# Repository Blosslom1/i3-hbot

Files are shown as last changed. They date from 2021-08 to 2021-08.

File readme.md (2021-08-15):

# 3Dimension Printer

## 机器简介

本项目中含有三台打印机结构。依次迭代更新。

i3进程&远程挤出结构，家用级，适合慢速打印，快速会出现较多震纹，精度普通最高达到0.1mm。

主控芯片采用的mega2560芯片，固件改写的为marlin1.1.9

驱动使用4个A4988（双z并联），可以根据自己经济能力改用TMC2209或闭环驱动。

hbot，高精工业级，可以实现高速打印在影响质量较小的情况下是i3速度的4-8倍速，最高精度可达0.025mm。主控是32位LPC1768，固件升级为marlin2.0.x

本hbot打印机是由上一版本i3结构改造，设计理念围绕低成本，高性能 ，在采购原始材料尽量使用的未加工的材料成本较低。

制作流程请跟随本文指示。

### 第一步

参看原始设计图，使用solid work2019，打开根目录的装配体1，看懂机械原理有大概机器布局印象后进行材料采购。

### 第二步

使用excel打开根目录BOM表。名称为i3_BOM（由于零件细碎未整理hbot的bom，仅仅增加几个2020铝型材大体没有怎么变）。

### 第三步

打印件定制，设计图纸的非标零件都需要定制，使用FMD打印定制即可，可以进入hbot打印件中查看需要定制的零件种类。

### 第四步

主板如果使用mega2560，使用arduino(先安装程序固件\arduino-1.8.13-windows.exe)写入程序固件中的程序程序目录：程序固件\Marlin-2.0.x\Marlin\Marlin.ino

主板使用skr等32位主板，使用卡烧录，firmware.bin文件，文件已经调试编译好可以直接烧录。

## 暂停更新

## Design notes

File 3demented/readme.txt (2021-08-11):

X固定×1
X固定右×1
Y光轴固定×4
Y同步轮固定×1
Y轴步进电机固定×1
Z轴固定×2
热床底板固定×4
挤出机支架×1
熔融喷头固定×1
Y固定上×2

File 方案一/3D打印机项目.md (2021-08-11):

# 3D打印机项目

## 打印机类型

熔融沉积型打印机（FDM）

## 设计建模

建模软件使用的是solid works 2018，用二维图形生成三维图形。

### 支架型材

#### x轴铝型材

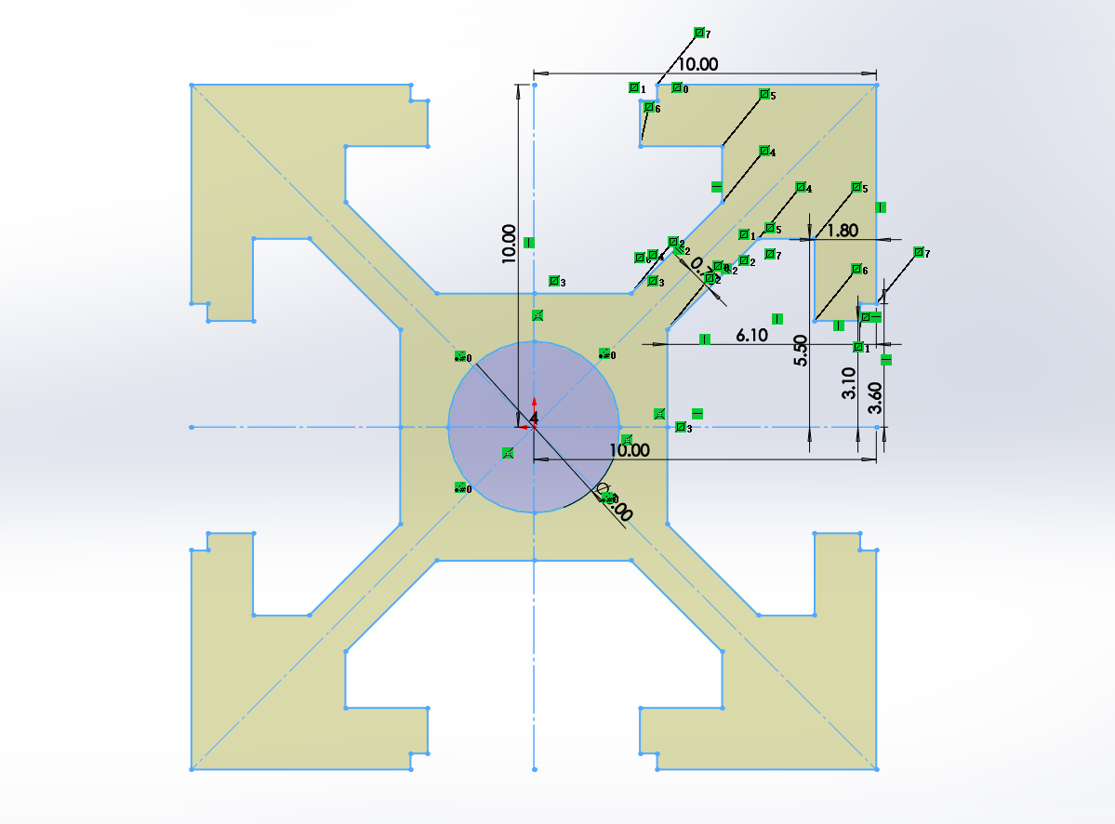
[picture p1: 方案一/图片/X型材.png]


规格如图（规格全部参考模型源文件，项目地址），使用拉伸凸台生成立体零件，拉伸长度是245mm

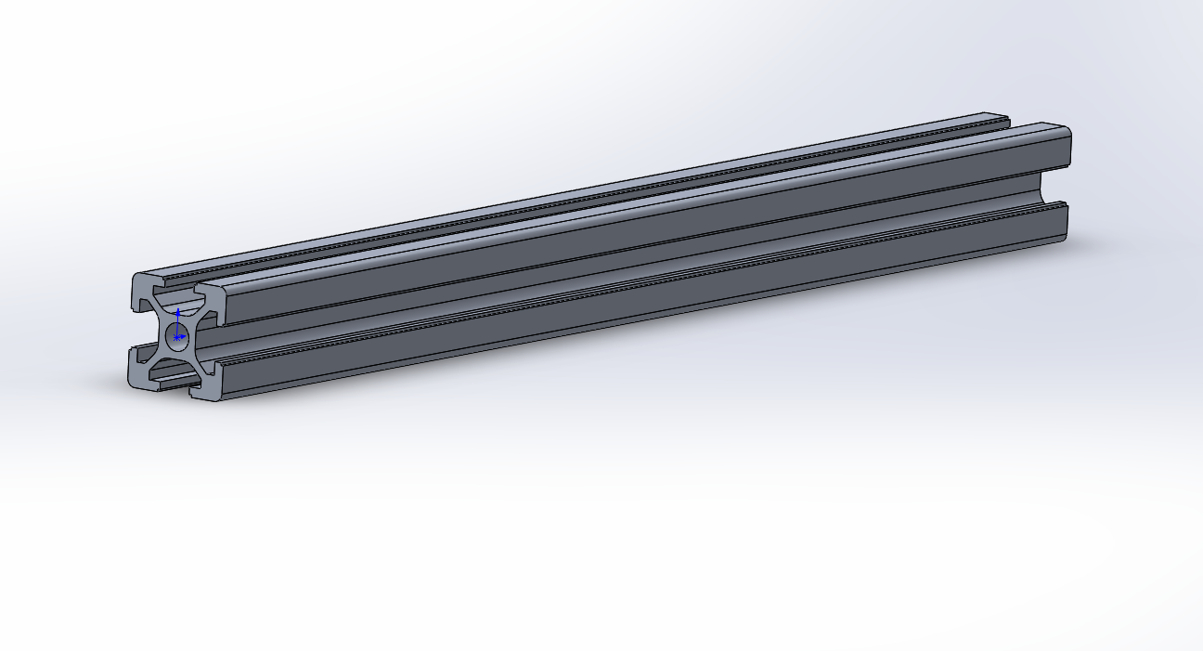
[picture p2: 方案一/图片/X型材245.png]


#### y轴铝型材

同x轴型材，拉伸长度是385mm

#### z轴铝型材

同x轴型材，拉伸长度是310mm

#### x光轴

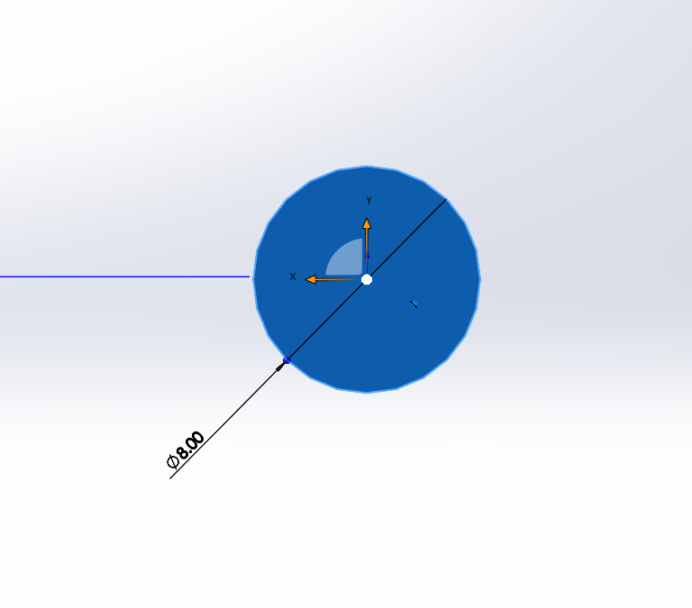
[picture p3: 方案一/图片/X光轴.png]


规格如图，使用拉伸凸台生成立体零件，拉伸长度是320mm

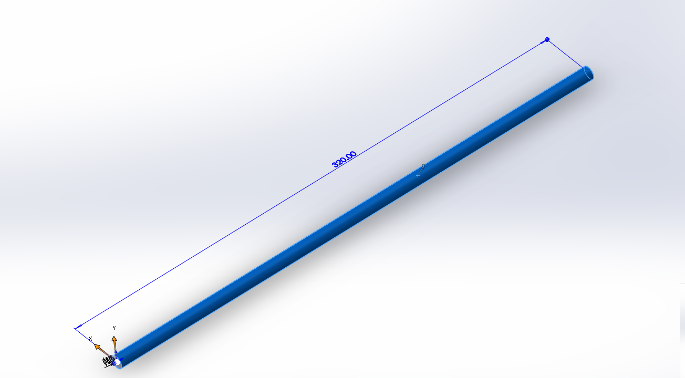
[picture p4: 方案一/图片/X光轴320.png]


#### y光轴

同x光轴，拉伸长度是380mm

#### z光轴

同x光轴，拉伸长度是345mm

#### z丝杆

长度305mm

#### 热床平台

下图为热床草图，厚度是3mm

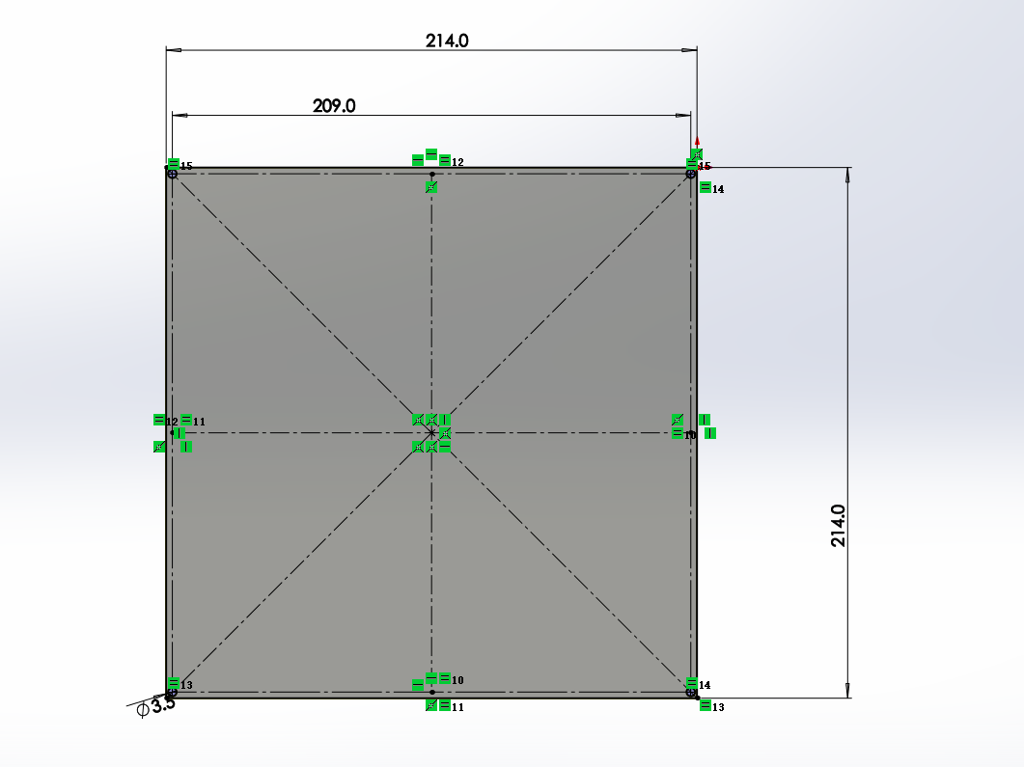
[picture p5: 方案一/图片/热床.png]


下图为热床地板草图，厚度是2.5mm

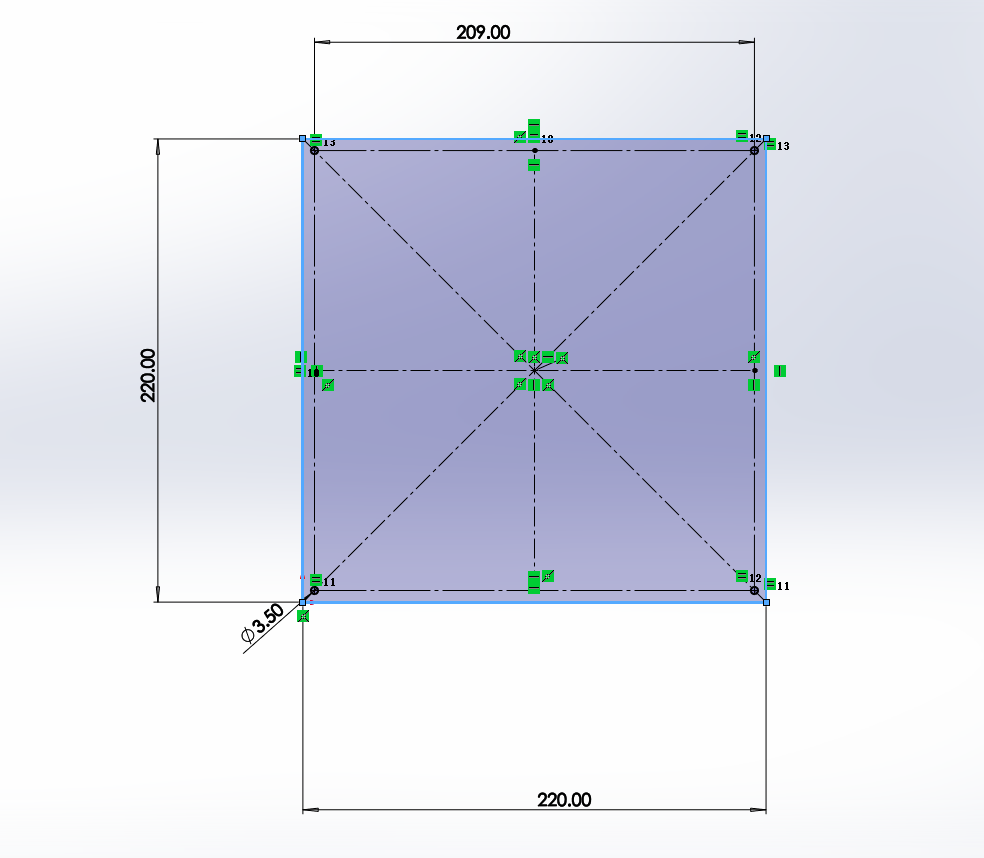
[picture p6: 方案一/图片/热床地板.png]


#### 角码

角码中间位置，L型型材，拉伸长度是20mm

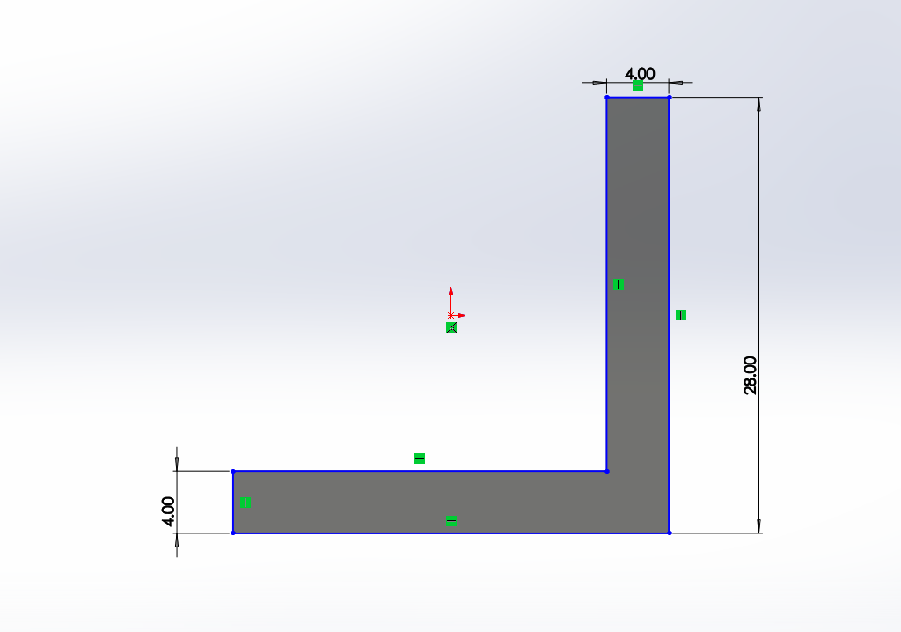
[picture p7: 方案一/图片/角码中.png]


角码侧边位置如图尺寸，两边通过镜像建立，拉伸长度是3.5mm

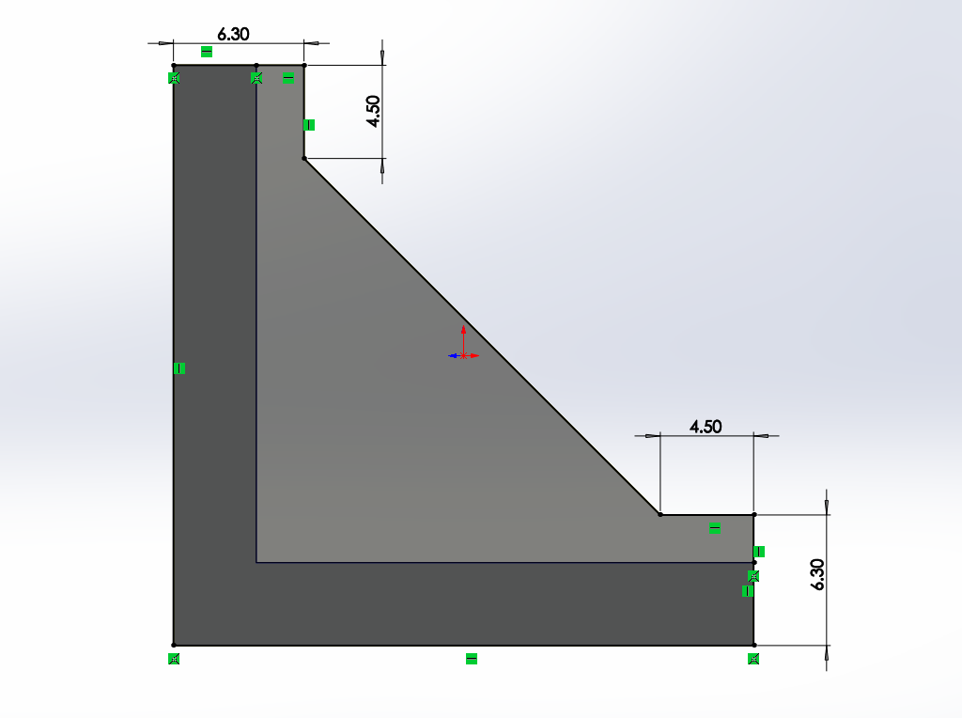
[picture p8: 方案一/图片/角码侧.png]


角码底和后面是一样的，拉伸切除，草图如下

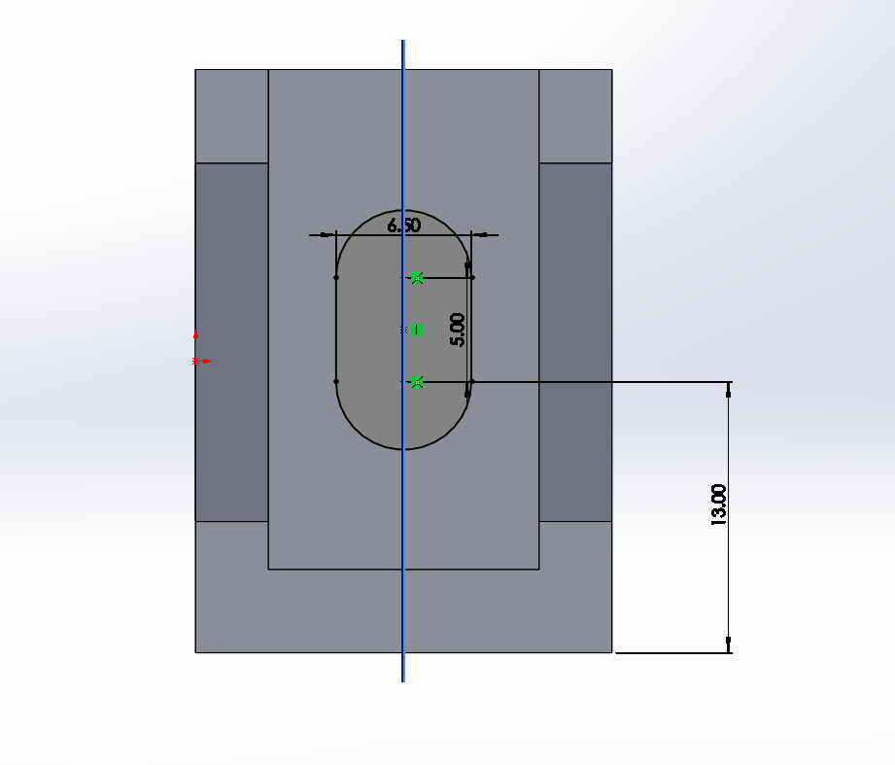
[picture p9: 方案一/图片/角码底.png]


整体图如下：

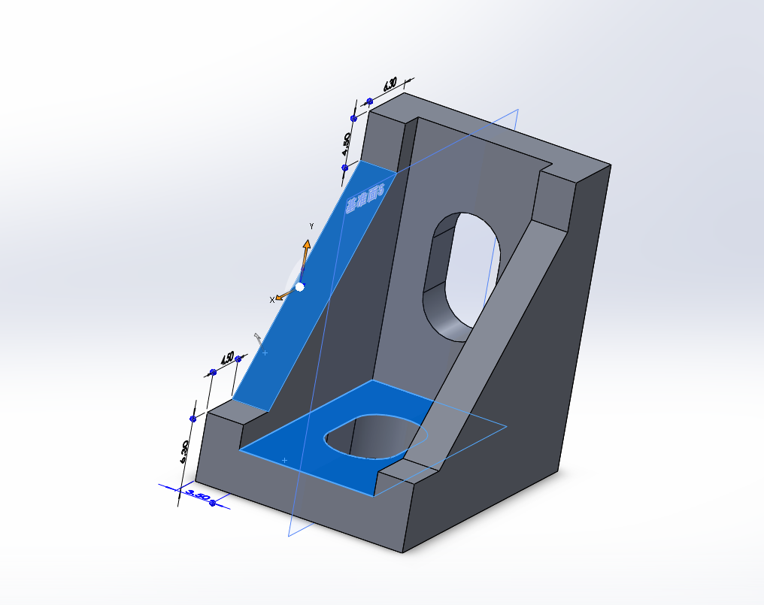
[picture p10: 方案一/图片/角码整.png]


#### 联轴器

联轴器是由一个圆柱体组成，中空，阶梯规格，草图如下，拉伸25mm

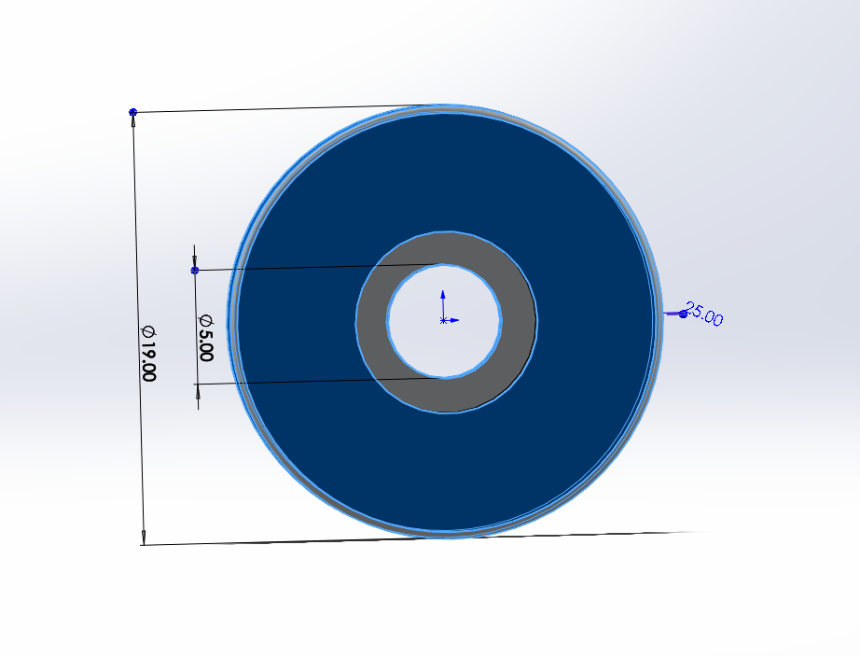
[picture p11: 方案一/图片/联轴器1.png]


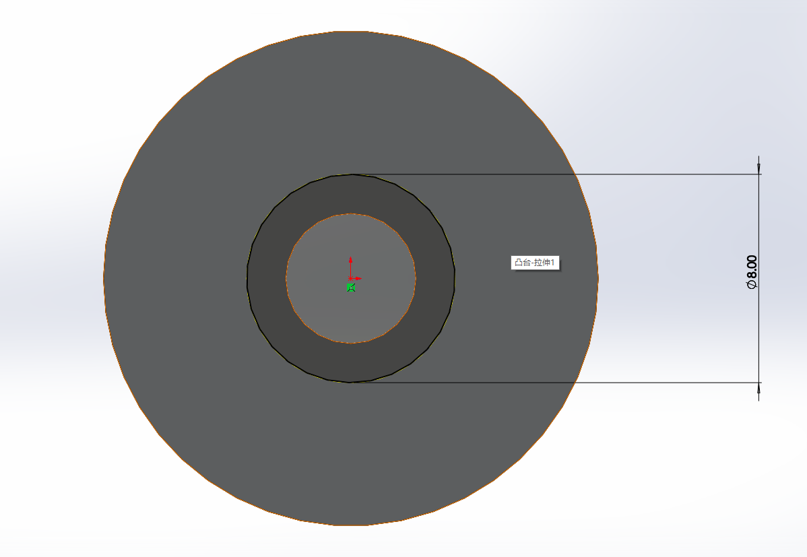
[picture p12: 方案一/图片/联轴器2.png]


整体如下图：

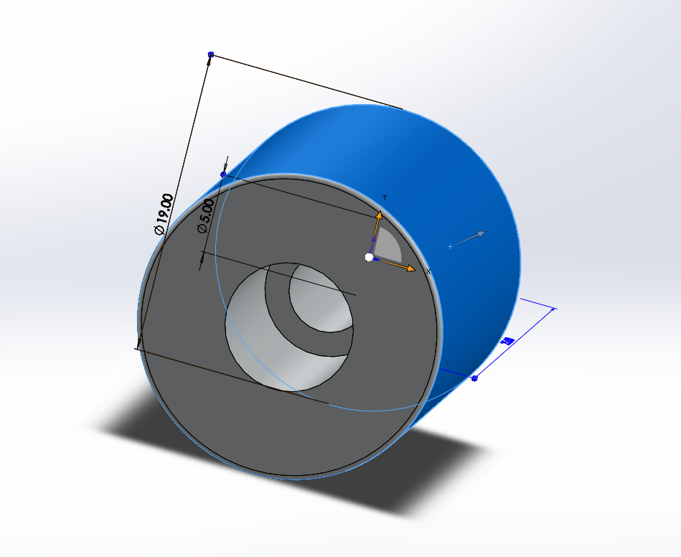
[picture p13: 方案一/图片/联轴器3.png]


#### 同步轮

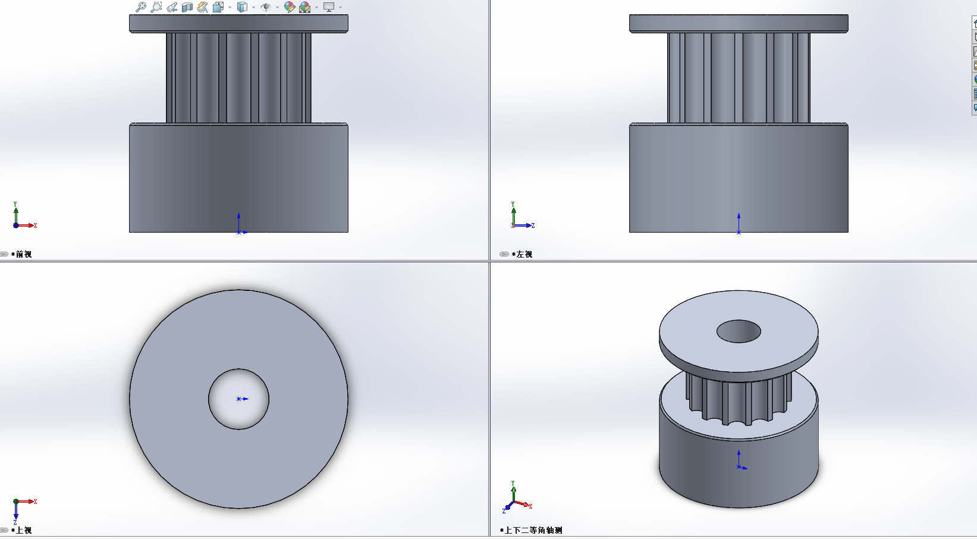
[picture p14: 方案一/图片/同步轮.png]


#### LM8UU

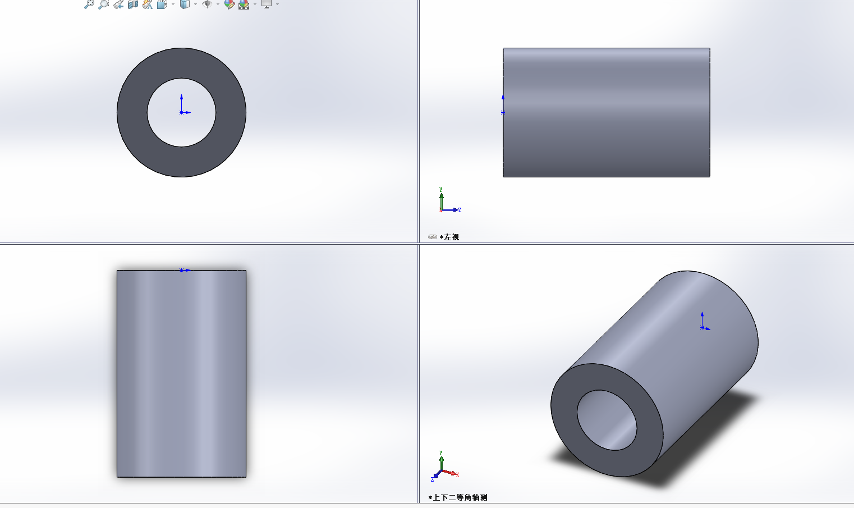
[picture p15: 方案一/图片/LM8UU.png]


#### 丝杆螺母

丝杆螺母，参考图。

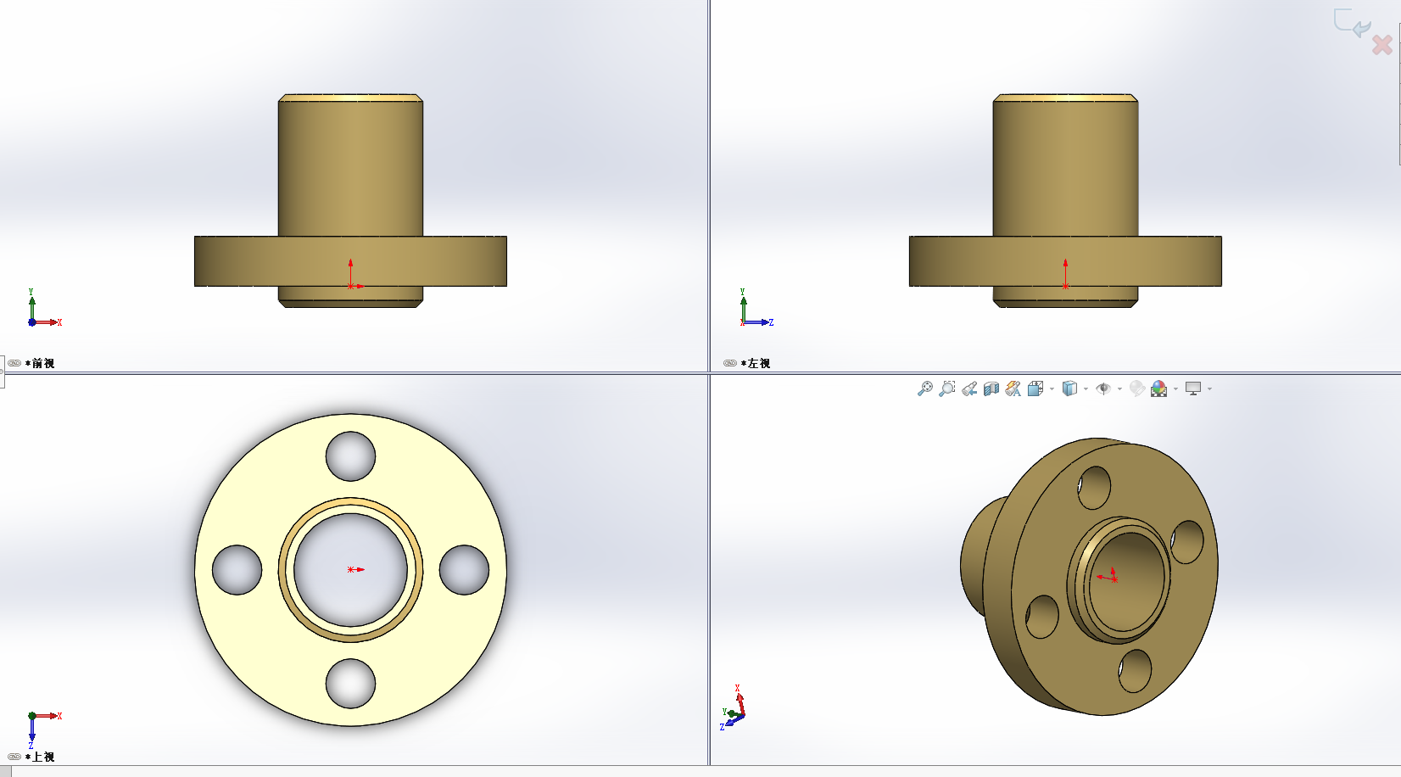
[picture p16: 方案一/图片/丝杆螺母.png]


#### 42步进电机

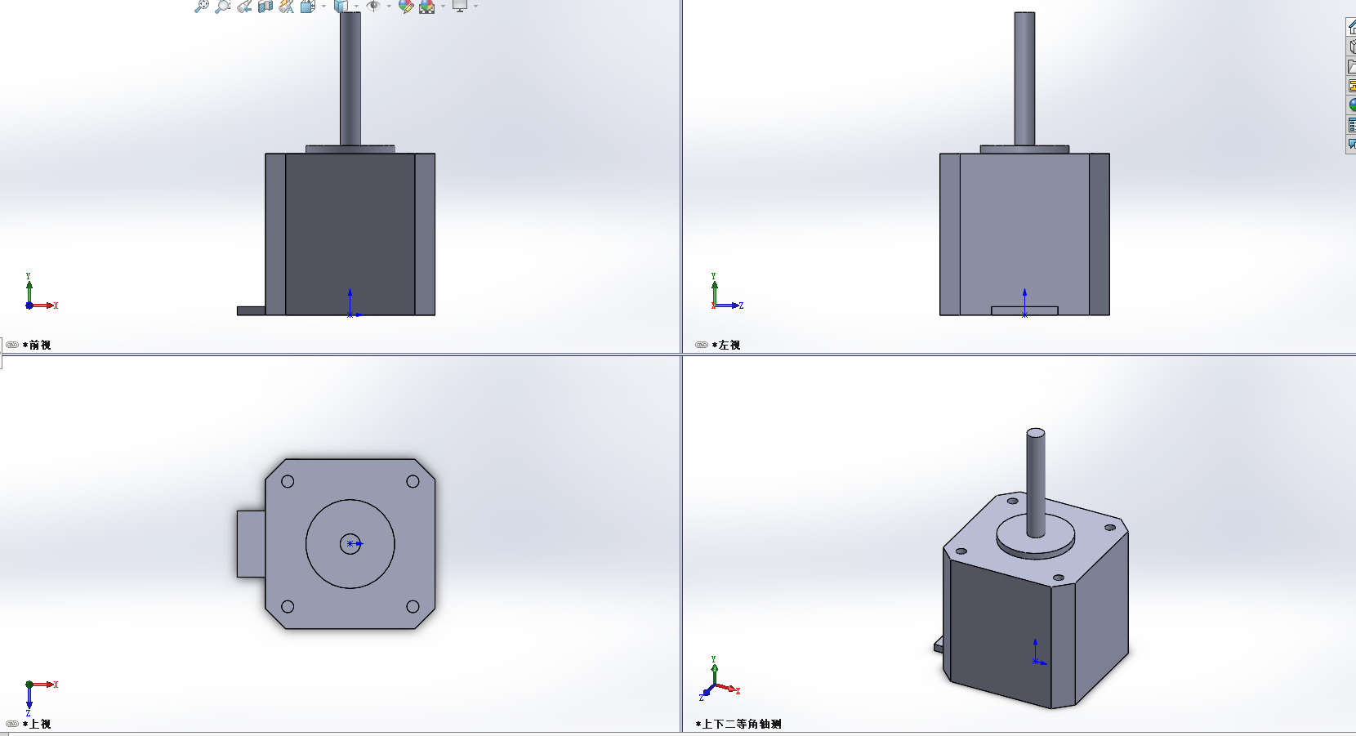
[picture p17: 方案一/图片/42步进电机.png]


#### 挤出机

下图是MK8底板。

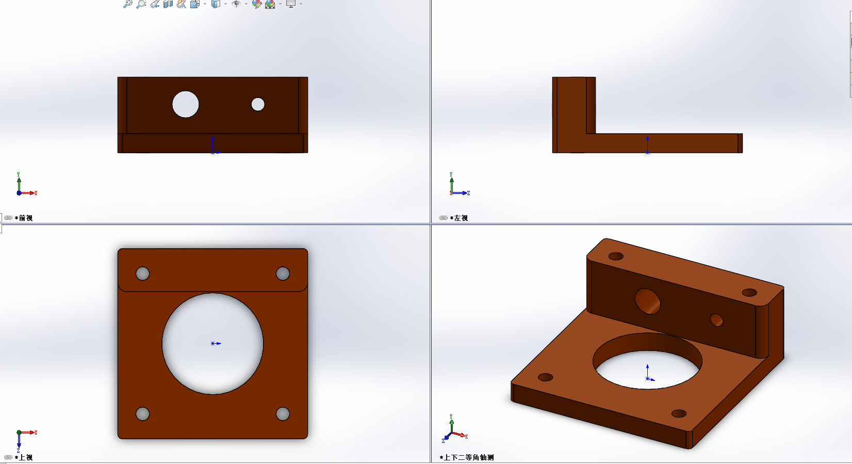
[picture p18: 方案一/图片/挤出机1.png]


下图是MK8压杆

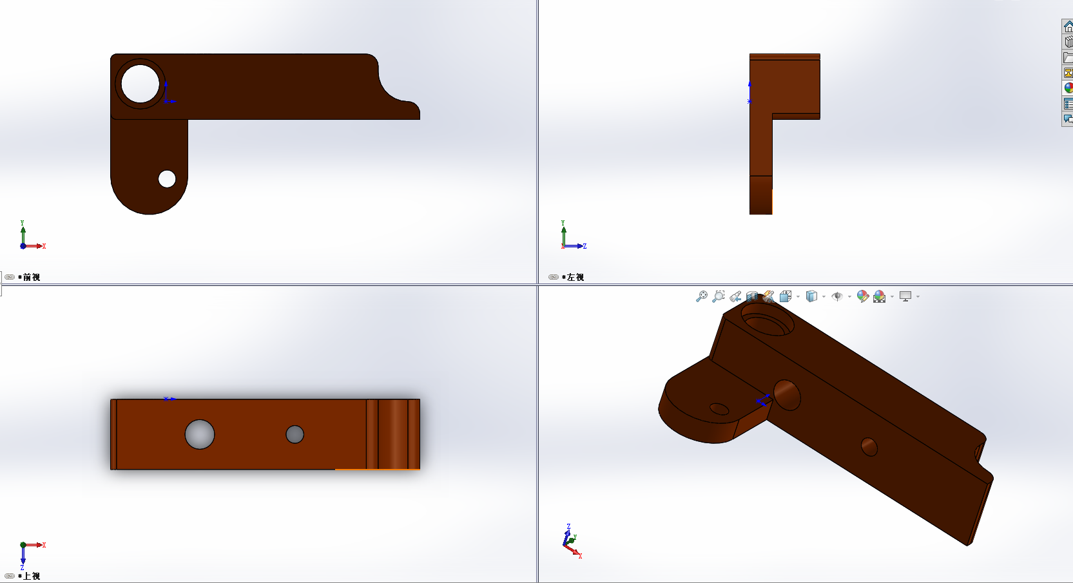
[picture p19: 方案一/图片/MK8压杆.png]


下图是MK8散热片

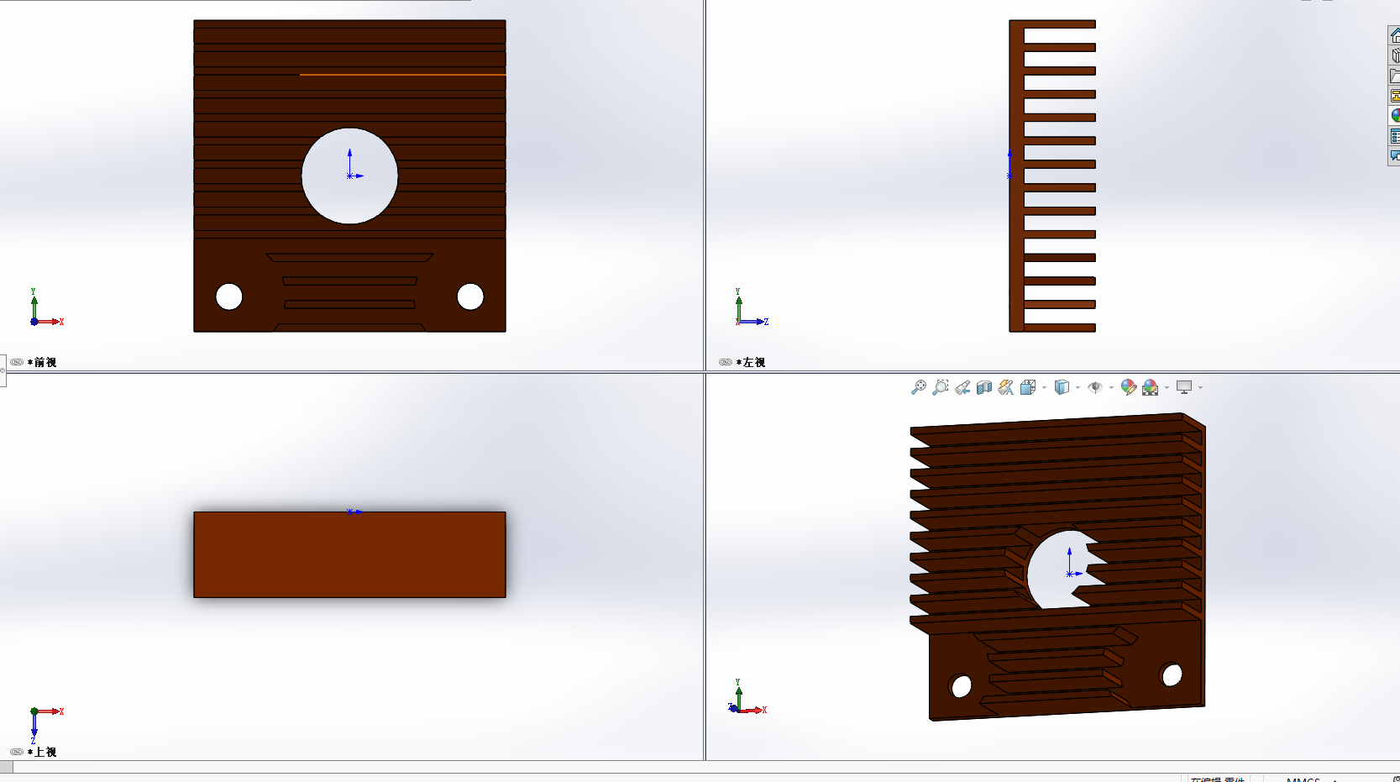
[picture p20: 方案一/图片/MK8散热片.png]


#### 喉管

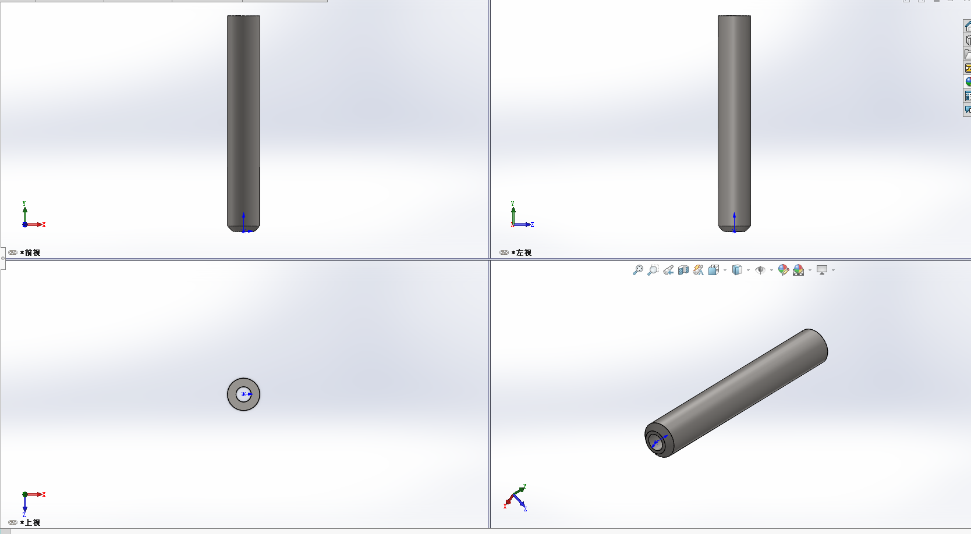
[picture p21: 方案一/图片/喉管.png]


#### 喉管散热片

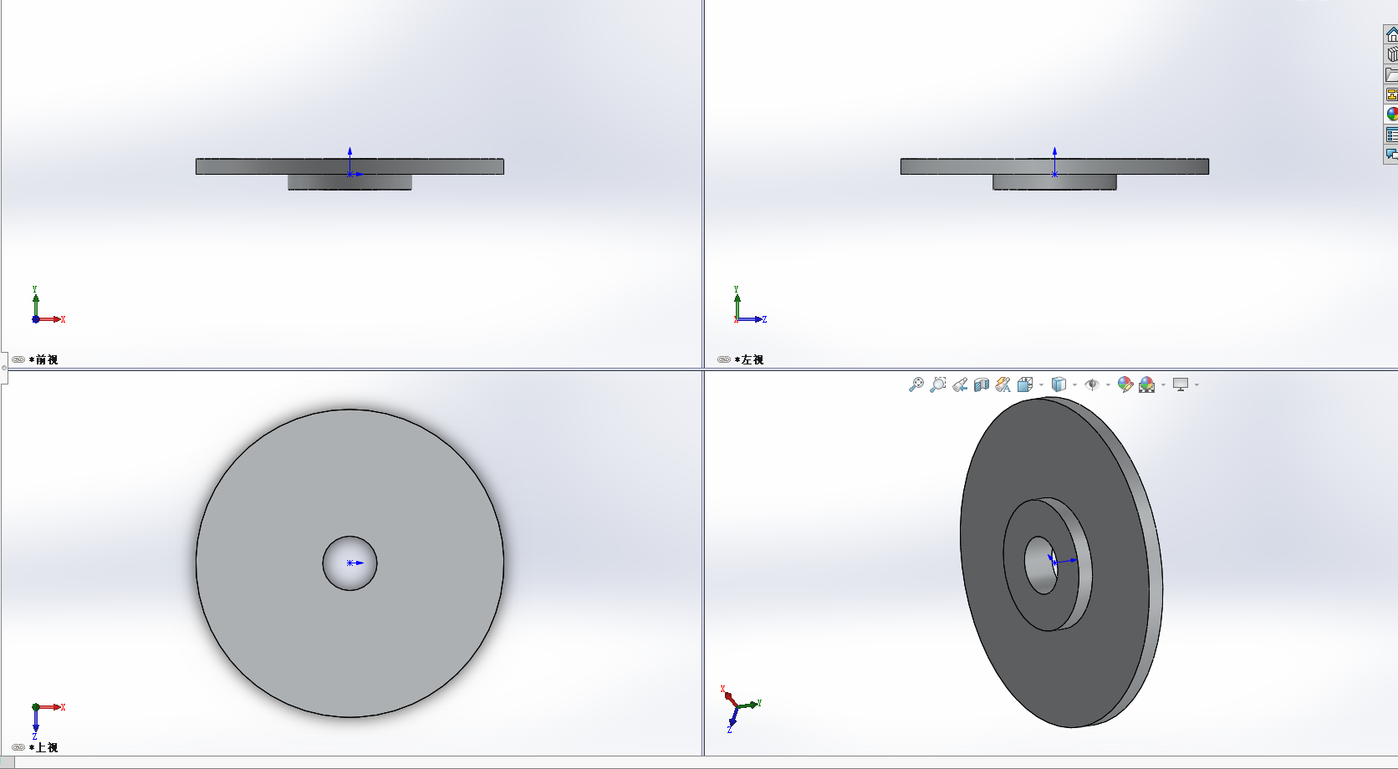
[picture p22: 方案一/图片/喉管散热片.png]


#### 固定

下图是Y光轴固定

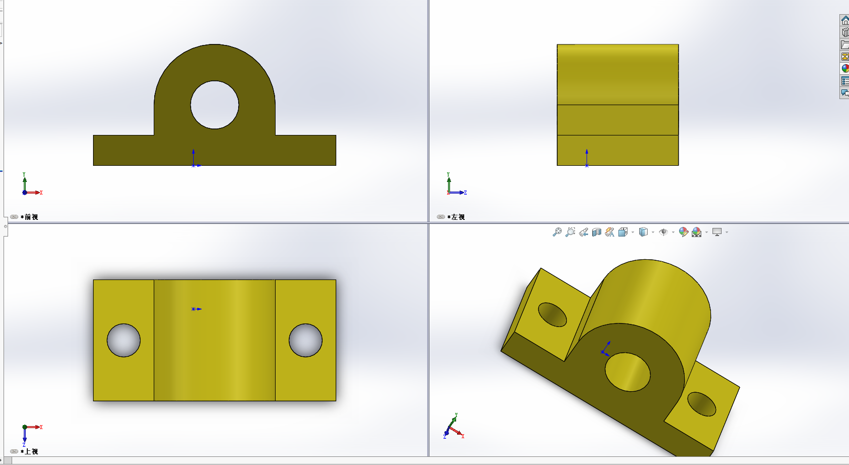
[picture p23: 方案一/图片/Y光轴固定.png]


下图是热床底板固定

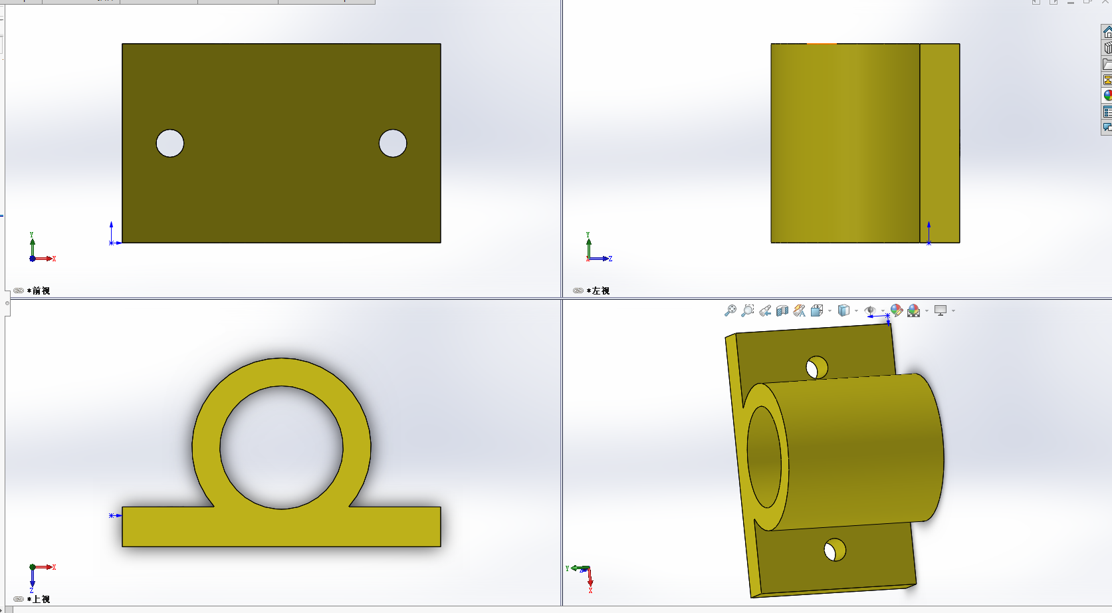
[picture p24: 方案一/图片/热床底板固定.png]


#### 铝加热块



#### 喷口



### 零件总装

使用装配界面将上面设计好的零件进行装配。

需要零件有X型材2个，角码4个，横梁型材1个，热床平台1个，光轴380两个，光轴固定4个，热床底板固定4个，LM8UU4个。下列是他们的几何位置关系。

{% hideBlock 查看几何位置关系 %} 

重合2X型材(1),Y型材(1)

重合5X型材(1),Y型材(1)

重合6X型材(1) ,Y型材(1)

重合8X型材(1),角码(1)

重合9Y型材(1),角码(1)

重合10X型材(1),角码(1)

重合15X型材(1) ,Y型材(2)

重合21X型材(1),Y型材(2)

重合22X型材(1),Y型材(2)

人重合24Y型材(2),角码(2)

重合25X型材(1),角码(2)

重合26Y型材(2) ,角码(2)

重合27角码(1),角码(2=

重合30Y型材(1),X型材(2)

重合31Y型材(1),X型材(2)

重合32Y型材(1),X型材(2)

重合33角码(4),X型材(2)

重合34Y型材(1),角码(4)

重合35Y型材(1),角码(4)

重合36角码(3) ,X型材(2)

重合37Y型材(2),角码(3)

重合38V型材(2),角码(3)

重合39Y型材(1),Z型材(1)

重合40Y型材(1),7型材(1)

重合43V型材(2),Z型材(2)

重合44Y型材(2),Z型材(2)

重合47Z型材(1),Z型材(2)

重合48Z型材(1),横梁型材(1)

重合49Z型材(1),横梁型材(1)

重合51Z型材(1),角码(5)

重合52横梁型材(1),角码(5)

重合53Z型材(1),角码(5)

重合55横梁型材(1),角码(6)

重合56Z型材(2),角码(6)

重合57Z型材(2),角码(6)

距离1横梁型材(1),Z型材(1)

重合58X型材(1),Y光轴固定(1)

重合59 X型材(1),Y光轴固定(1)

同心1Y光轴380(1),Y光轴固定(1)

重合62Y光轴380(1),Y光轴固定(1)

重合63X型材(1),Y光轴固定(2)

重合64X型材(1),Y光轴固定(2)

同心2Y光轴固定(2),Y光轴380(2)

重合66Y光轴固定(2),Y光轴380(2)

重合69 X型材(2),Y光轴固定(4)

重合70X型材(2),Y光轴固定(4)

同心3Y光轴380(2) ,Y光轴固定(4)

重合72X型材(2),Y光轴固定(5)

重合73X型材(2),Y光轴固定(5)

同心4Y光轴380(1),Y光轴固定(5)

同心5Y光轴380(2),LM8UU(3=

同心6Y光轴380(2),LM8UU(4)

同心7Y光轴380(1),LM8UU(2)

同心8Y光轴38O(1),LM8UU(1)

重合76 LM8UU(2),热床底板固定(1)

同心9LM8UU(2),热床底板固定(1)

重合77 LM8UU(4),热床底板固定(3)

同心10 LM8UU(4),热床底板固定(3)

重合78LM8UU(3) ,热床底板固定(4)

同心11 LM8UU(3),热床底板固定(4)

重合79 LM8UU(1),热床底板固定(5)

同心12LM8UU(1),热床底板固定(5)

同心15热床平台(1),热床底板固定(3)

同心16热床平台(1),热床底板固定(3)

同心17热床平台(1),热床底板固定(1)

同心18热床平台(1),热床底板固定(1)

同心19热床平台(1),热床底板固定(4)

同心20热床平台(1),热床底板固定(4)

重合82热床平台(1),热床底板固定(4)

同心21热床平台(1),热床底板固定(5)

同心22热床平台(1),热床底板固定(5)

重合83热床平台(1),热床底板固定(1)

{% endhideBlock %}



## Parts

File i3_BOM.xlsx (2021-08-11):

名称 | 型号 | 单价 | 数量 | 总价
光轴8mm | x350mm | 3.62 | 2 | 7.24
 | y390mm | 5.25 | 2 | 10.5
 | z350 | 4.25 | 2 | 8.5
MK3铝基板热床 | 220*220*3 | 37 | 1 | 37
X型材 | x250mm | 6 | 2 | 12
 | y390mm | 6 | 2 | 12
 | z320mm | 6 | 2 | 12
 | 横梁400mm | 9 | 1 | 9
螺杆导成8 | 350mm | 12.2 | 2 | 24.4
角码 | 20*28mm | 1.25 | 14 | 17.5
42步进电机 | 泰坦挤出机 | 12.8 | 1 | 12.8
 | 38mm | 12.8 | 3 | 38.4
 | 48二手 | 12.8 | 1 | 12.8
联轴器 | 5*8 | 1.69 | 2 | 3.38
直线轴承 | 8*15*24 | 1.42 | 12 | 17.04
同步轮 | 20齿 | 1 | 2 | 2
惰轮 | 20齿 | 2.3 | 2 | 4.6
同步带 | 6mm*2m | 4.75 | 1 | 4.75
滚动轴承 | 8*22*7 | 0.26 | 2 | 0.52
CR8散热管 | 红色 | 3.8 | 1 | 3.8
铁氟龙管 | 2*4 | 2.2 | 1 | 2.2
气动插头 | M6 | 0.6 | 1 | 0.6
CR10远程挤出机 | 红色 | 11 | 1 | 11
E3D铝加热块 | MK8 | 0.45 | 1 | 0.45
散热风扇 | 12V | 2 | 2 | 4
风扇保护架 | 40*40 | 0.55 | 2 | 1.1
喷头 | 黄铜0.3 | 0.2 | 1 | 0.2
喉管 | E3D | 0.5 | 1 | 0.5
硅胶 |  | 3.7 | 1 | 3.7
电源 | 12V20A250W | 38 | 1 | 38
加热管 | 12V40W | 1.55 | 1 | 1.55
热敏电阻 | 200℃ | 1.78 | 1 | 1.78
arduino | MEGA2560 R3 | 37.8 | 1 | 37.8
拓展板 | RAMPS1.4 | 13.8 | 1 | 13.8
步进电机驱动板 | A4988 | 3 | 5 | 15
显示屏 | 12864LCD | 30 | 1 | 30
铝板 | 220*220 | 13 | 1 | 13
螺丝 | M3多种长度 | 4 | 5 | 20
尼龙轧带 | 4*200 | 4.5 | 1 | 4.5
固定件 | 建模定制 | 30 | 1 | 30
总价 |  |  |  | 479.41

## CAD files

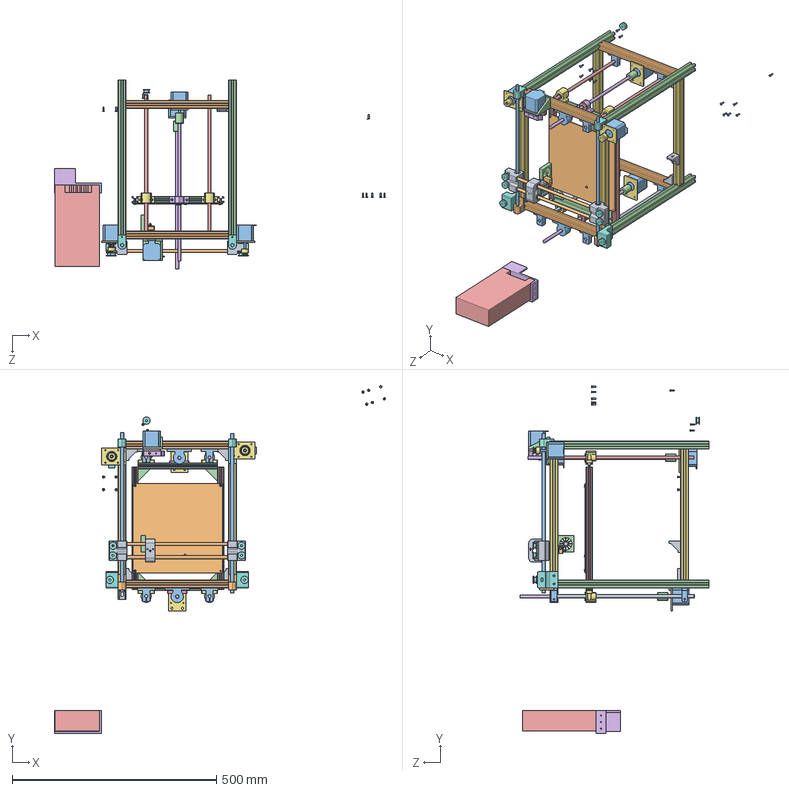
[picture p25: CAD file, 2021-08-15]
装配体1.SLDASM
811.5 x 852.4 x 463.7 mm
X光轴320 x 2
X型材250 x 4
Y光轴390 x 2
Y型材390 x 3
Z光轴350 x 2
Z丝杆350 x 2
Z型材320 x 4
横梁型材350
角码 x 6
热床
42步进电机 x 5
联轴器 x 2
丝杆螺母 x 2
LM8UU x 10
同步轮 x 2
惰轮 x 7
轴承 x 2
M3螺丝 x 4
M3螺丝8m x 14
挤出机支架
MK8底板
MK8压杆
喉管散热
喉管
气动插头
铝加热块
喷口
风扇
电源
电源支座
铝合金步进电机固定 x 4
y的光轴固定 x 2
x光轴固定 x 2
光轴250. x 2
SK8 x 8
热床x x 2
热床y x 2
丝杆固定
光轴固定 x 4
惰轮固定 x 2
x滑块
y的光轴固定反 x 2
628zz固定 x 2
打印角码 x 4
丝杆固定2

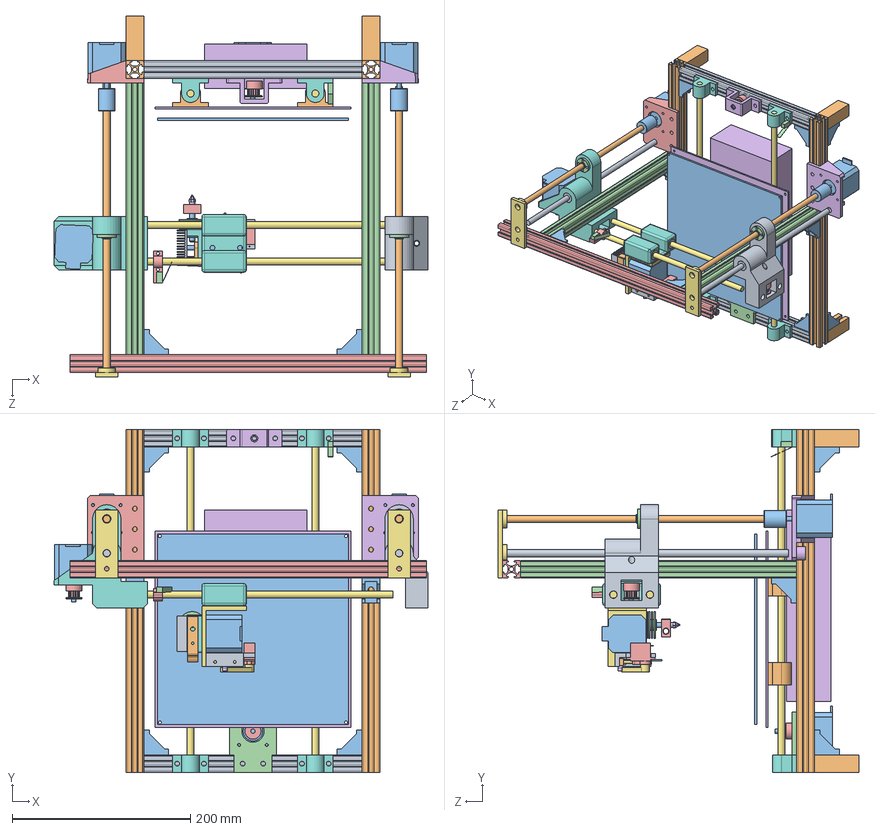
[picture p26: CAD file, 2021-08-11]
方案一/总装 - 备份2.SLDASM
419.1 x 385.0 x 405.0 mm
X型材 x 2
Y型材 x 2
角码 x 12
Z型材 x 2
横梁型材
热床平台
Y光轴380 x 2
Y光轴固定 x 4
LM8UU x 12
热床底板固定 x 4
42步进电机 x 5
Y轴步进电机固定
同步轮 x 4
Y同步轮固定
X光轴320 x 2
打印头固定
MK8散热片
MK8压杆
喉管
喉管散热片 x 4
铝加热块
喷口
挤出机支架
MK8底板
Z光轴345 x 2
Z丝杆305 x 2
联轴器 x 2
丝杆螺母 x 2
z电机支架
z电机支架B
z丝杆固定 x 2
z滑块左侧
z滑块右侧
立柱 x 4
热床
微动开关 x 2
X限位固定 x 2
电源
M3光轴 x 2
光耦
调平底板
调平滑块
探针
调平遮挡
舵机
MR63ZZ x 2
调平拨杆

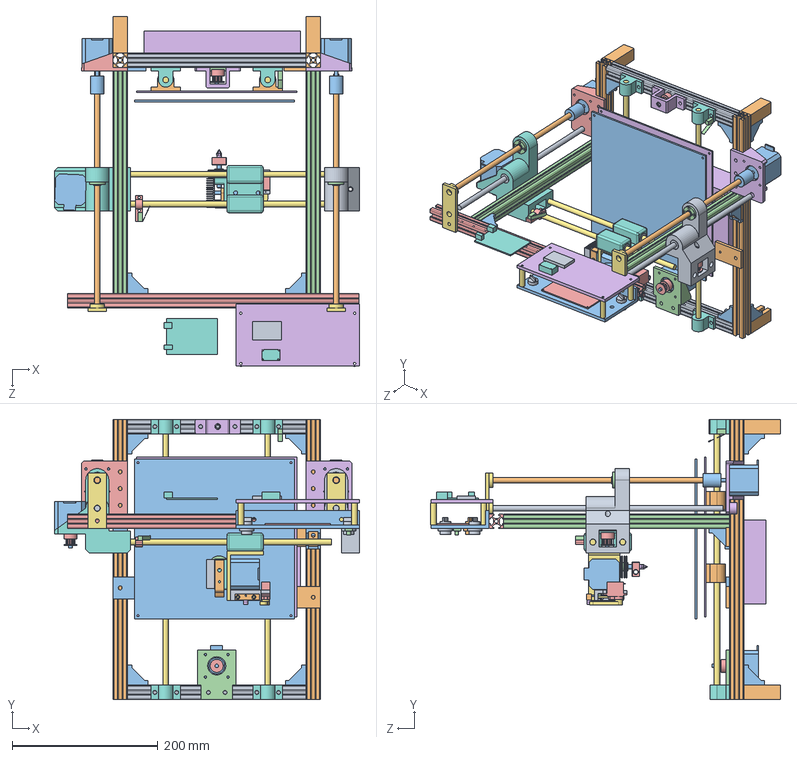
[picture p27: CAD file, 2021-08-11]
方案一/总装.SLDASM
419.2 x 385.0 x 480.5 mm
X型材 x 2
Y型材 x 2
角码 x 12
Z型材 x 2
横梁型材
热床平台
Y光轴380 x 2
Y光轴固定 x 4
LM8UU x 12
热床底板固定 x 4
42步进电机 x 5
Y轴步进电机固定
同步轮 x 4
Y同步轮固定
X光轴320 x 2
打印头固定
MK8散热片
MK8压杆
喉管
喉管散热片 x 4
铝加热块
喷口
挤出机支架
MK8底板
Z光轴345 x 2
Z丝杆305 x 2
联轴器 x 2
丝杆螺母 x 2
z电机支架
z电机支架B
z丝杆固定 x 2
z滑块左侧
z滑块右侧
立柱 x 4
热床
微动开关 x 2
X限位固定 x 2
电源
M3光轴 x 2
光耦
调平底板
调平滑块
探针
调平遮挡
舵机
MR63ZZ x 2
调平拨杆
ArduinoMega
按钮红 x 2
按钮绿
控制面板
旋转编码器
12864显示屏
背板
背板立柱 x 4
继电器
读卡器
电源挂架A x 2
电源挂架B

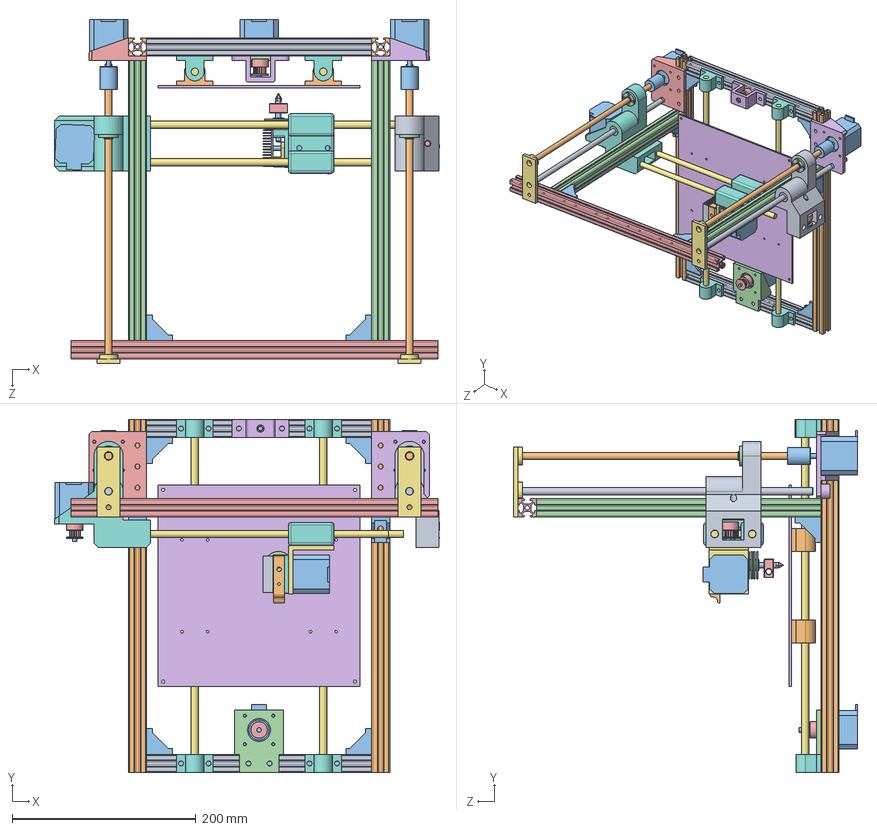
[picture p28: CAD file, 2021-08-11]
方案一/总装 - 备份.SLDASM
419.6 x 385.0 x 375.0 mm
X型材 x 2
Y型材 x 2
角码 x 8
Z型材 x 2
横梁型材
热床平台
Y光轴380 x 2
Y光轴固定 x 4
LM8UU x 12
热床底板固定 x 4
42步进电机 x 5
Y轴步进电机固定
同步轮 x 4
Y同步轮固定
X光轴320 x 2
打印头固定
MK8散热片
MK8压杆
喉管
喉管散热片 x 4
铝加热块
喷口
挤出机支架
MK8底板
Z光轴345 x 2
Z丝杆305 x 2
联轴器 x 2
丝杆螺母 x 2
z电机支架
z电机支架B
z丝杆固定 x 2
z滑块左侧
z滑块右侧

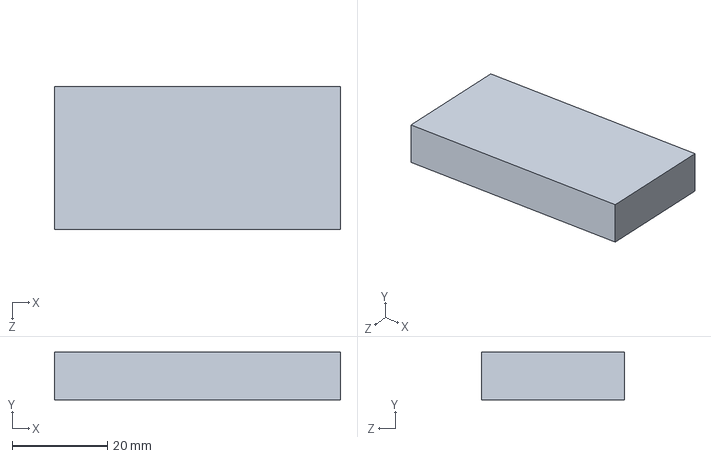
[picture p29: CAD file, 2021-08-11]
3demented/Y固定上.SLDPRT
60.0 x 10.0 x 30.0 mm

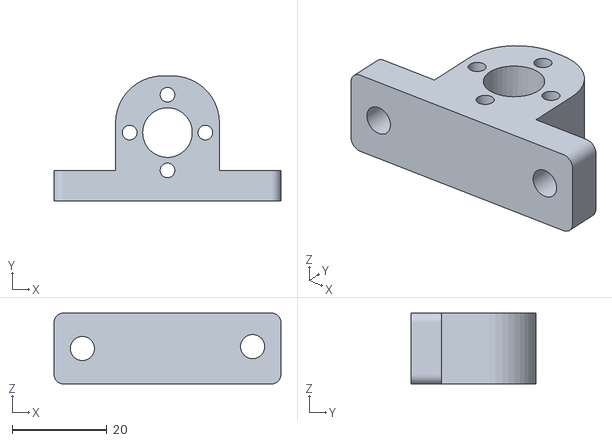
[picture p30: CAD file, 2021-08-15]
hbot打印件/丝杆固定2.STL
48.0 x 26.5 x 15.0

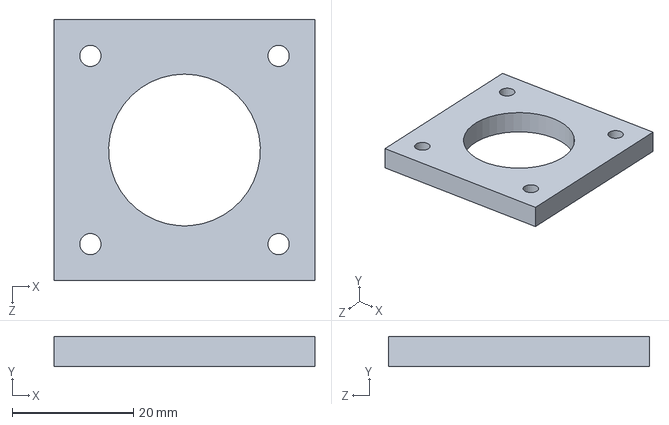
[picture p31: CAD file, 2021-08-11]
方案一/传动设备/Y轴步进电机固定.SLDPRT
43.0 x 5.00 x 43.0 mm

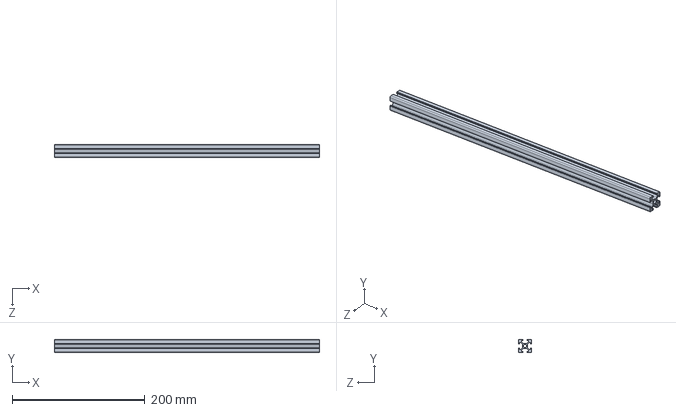
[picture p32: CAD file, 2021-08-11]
方案一/支架/横梁型材.SLDPRT
400.0 x 20.0 x 20.0 mm

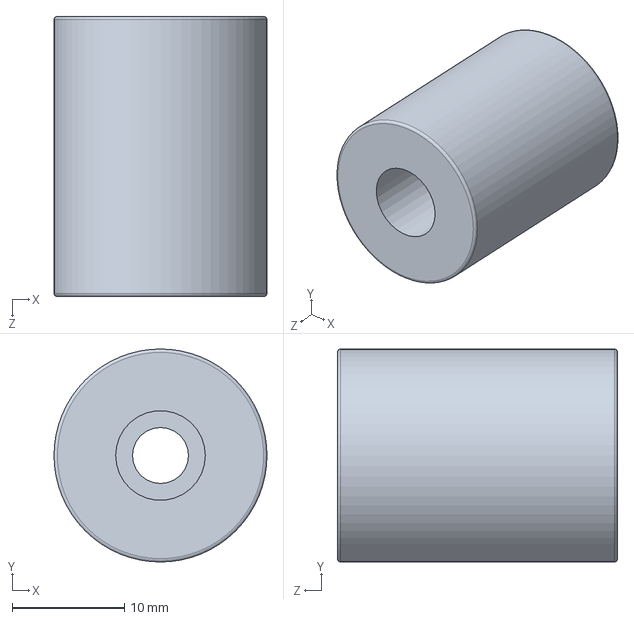
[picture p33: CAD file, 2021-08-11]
方案一/支架螺丝/联轴器.SLDPRT
19.0 x 19.0 x 25.0 mm

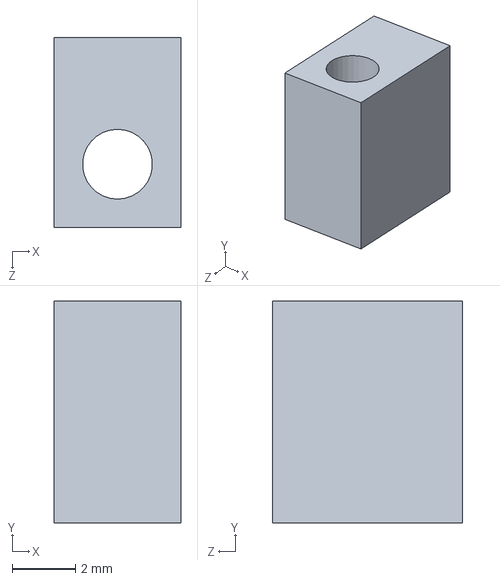
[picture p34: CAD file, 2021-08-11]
方案一/调平遮挡.SLDPRT
4.00 x 7.00 x 6.00 mm

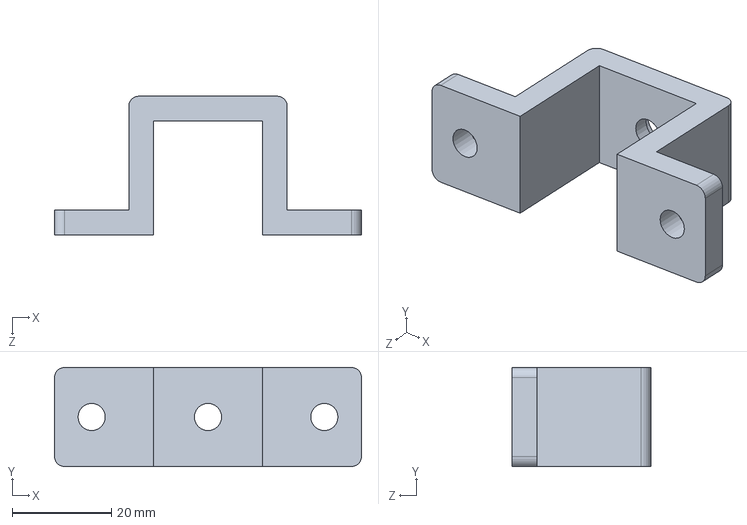
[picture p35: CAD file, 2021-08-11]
3demented/Y同步轮固定.SLDPRT
62.0 x 20.0 x 28.0 mm

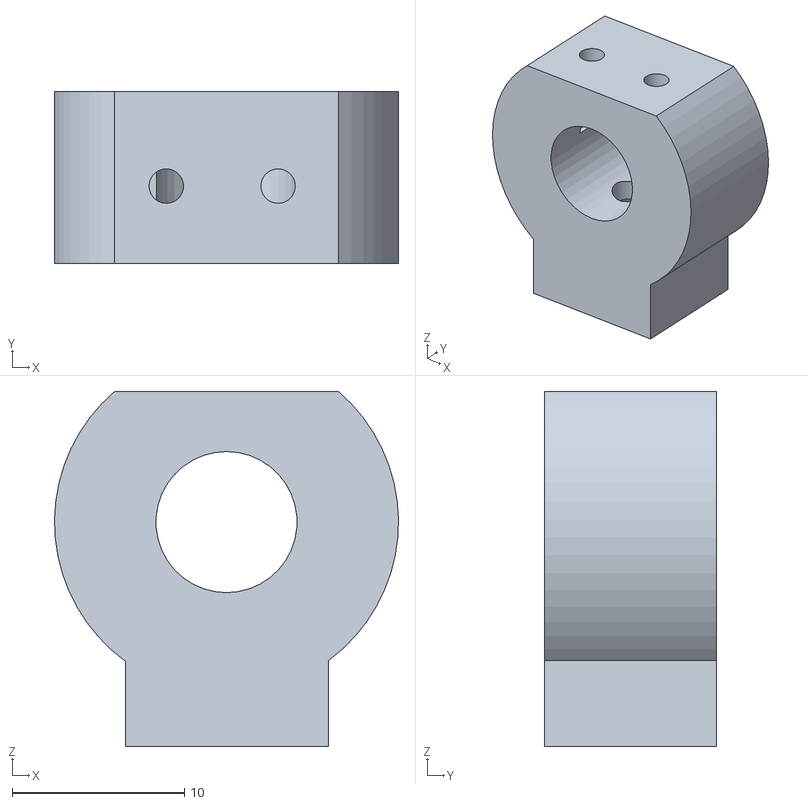
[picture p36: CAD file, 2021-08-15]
hbot打印件/限位固定.STL
20.0 x 10.0 x 20.7

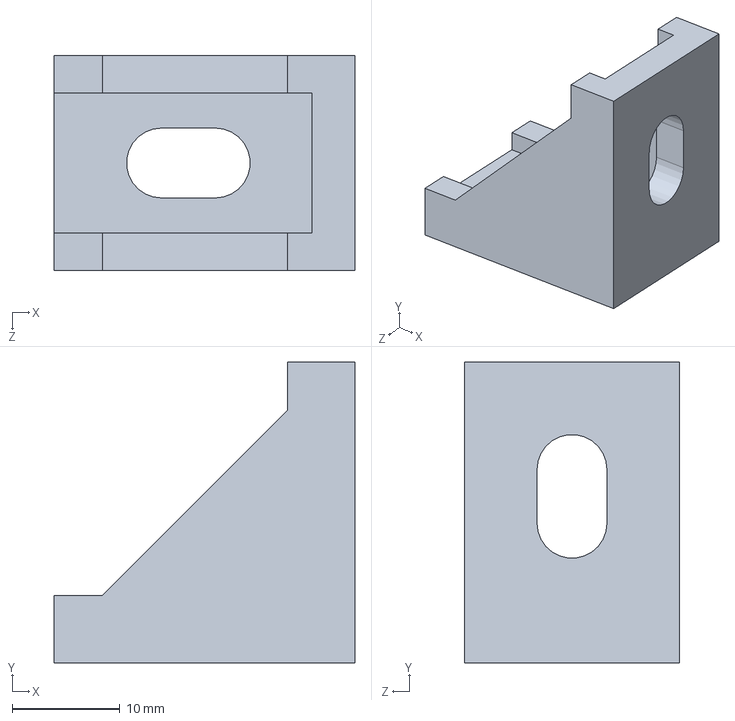
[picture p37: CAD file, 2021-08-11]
方案一/传动设备/角码.SLDPRT
28.0 x 28.0 x 20.0 mm

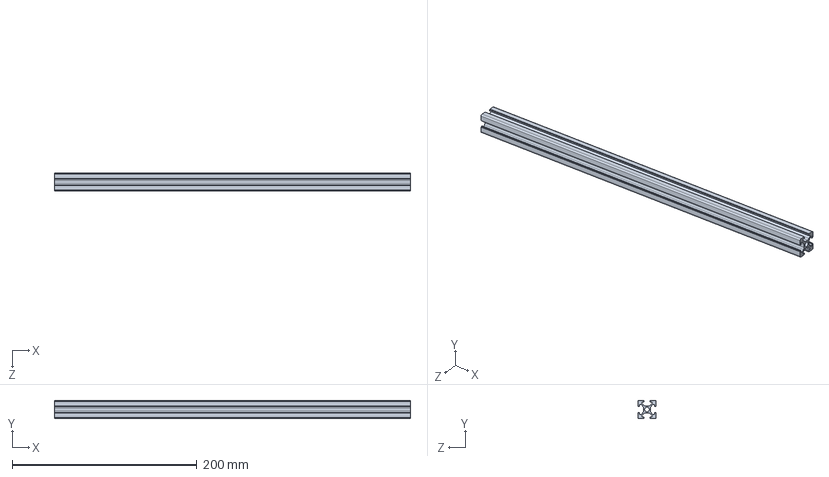
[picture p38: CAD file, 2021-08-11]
方案一/支架/Y型材.SLDPRT
385.0 x 20.0 x 20.0 mm

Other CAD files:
方案二/.DWG
方案一/工程图/Y轴步进电机固定.DWG
方案一/支架螺丝/LM8UU.SLDPRT
限位固定.SLDPRT
3demented/X固定.SLDPRT
3demented/X固定.STL
3demented/X固定右.SLDPRT
3demented/X固定右.STL
3demented/Y光轴固定.SLDPRT
3demented/Y光轴固定.STL
3demented/Y同步轮固定.STL
3demented/Y固定上.STL
3demented/Y轴步进电机固定.SLDPRT
3demented/Y轴步进电机固定.STL
3demented/Z轴固定.SLDPRT
3demented/Z轴固定.STL
3demented/挤出机支架.SLDPRT
3demented/挤出机支架.STL
3demented/热床底板固定.SLDPRT
3demented/热床底板固定.STL
3demented/熔融喷头固定.SLDPRT
3demented/熔融喷头固定.STL
42步进电机.SLDPRT
628zz固定.SLDPRT
LM8UU.SLDPRT
M3螺丝.SLDPRT
M3螺丝8m.SLDPRT
MK8压杆.SLDPRT
MK8底板.SLDPRT
SK8.SLDPRT
X光轴320.SLDPRT
X固定.SLDPRT
X固定右.SLDPRT
X固定右.STL
X型材250.SLDPRT
Y光轴390.SLDPRT
Y光轴固定.SLDPRT
Y固定上.SLDPRT
Y型材390.SLDPRT
Y轴步进电机固定.SLDPRT
Z丝杆350.SLDPRT
Z光轴350.SLDPRT
Z型材320.SLDPRT
Z轴固定.SLDPRT
hbot打印件/628zz固定.STL
hbot打印件/x光轴固定.STL
hbot打印件/x滑块.STL
hbot打印件/y的光轴固定.STL
hbot打印件/y的光轴固定反.STL
hbot打印件/丝杆固定.STL
hbot打印件/光轴固定.STL
hbot打印件/底座2.STL
hbot打印件/惰轮固定.STL
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

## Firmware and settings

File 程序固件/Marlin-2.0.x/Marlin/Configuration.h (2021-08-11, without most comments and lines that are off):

#pragma once
#define CONFIGURATION_H_VERSION 020006
#define STRING_CONFIG_H_AUTHOR "Blosslom's 3D printer" // Who made the changes.
#define SHOW_BOOTSCREEN
#define SERIAL_PORT -1
#define SERIAL_PORT_2 0
#define BAUDRATE 115200
  #define MOTHERBOARD BOARD_BTT_SKR_V1_3
#define CUSTOM_MACHINE_NAME "Blosslom's 3D printer"
#define EXTRUDERS 1
#define DEFAULT_NOMINAL_FILAMENT_DIA 1.75
#define TEMP_SENSOR_0 1
#define TEMP_SENSOR_1 0
#define TEMP_SENSOR_2 0
#define TEMP_SENSOR_3 0
#define TEMP_SENSOR_4 0
#define TEMP_SENSOR_5 0
#define TEMP_SENSOR_6 0
#define TEMP_SENSOR_7 0
#define TEMP_SENSOR_BED 1
#define TEMP_SENSOR_PROBE 0
#define TEMP_SENSOR_CHAMBER 0
#define DUMMY_THERMISTOR_998_VALUE 25
#define DUMMY_THERMISTOR_999_VALUE 100
#define MAX_REDUNDANT_TEMP_SENSOR_DIFF 10
#define TEMP_RESIDENCY_TIME     10  // (seconds) Time to wait for hotend to "settle" in M109
#define TEMP_WINDOW              1  // (°C) Temperature proximity for the "temperature reached" timer
#define TEMP_HYSTERESIS          3  // (°C) Temperature proximity considered "close enough" to the target
#define TEMP_BED_RESIDENCY_TIME 10  // (seconds) Time to wait for bed to "settle" in M190
#define TEMP_BED_WINDOW          1  // (°C) Temperature proximity for the "temperature reached" timer
#define TEMP_BED_HYSTERESIS      3  // (°C) Temperature proximity considered "close enough" to the target
#define HEATER_0_MINTEMP   5
#define HEATER_1_MINTEMP   5
#define HEATER_2_MINTEMP   5
#define HEATER_3_MINTEMP   5
#define HEATER_4_MINTEMP   5
#define HEATER_5_MINTEMP   5
#define HEATER_6_MINTEMP   5
#define HEATER_7_MINTEMP   5
#define BED_MINTEMP        5
#define HEATER_0_MAXTEMP 275
#define HEATER_1_MAXTEMP 275
#define HEATER_2_MAXTEMP 275
#define HEATER_3_MAXTEMP 275
#define HEATER_4_MAXTEMP 275
#define HEATER_5_MAXTEMP 275
#define HEATER_6_MAXTEMP 275
#define HEATER_7_MAXTEMP 275
#define BED_MAXTEMP      150
#define PIDTEMP
#define BANG_MAX 255     // Limits current to nozzle while in bang-bang mode; 255=full current
#define PID_MAX BANG_MAX // Limits current to nozzle while PID is active (see PID_FUNCTIONAL_RANGE below); 255=full current
#define PID_K1 0.95      // Smoothing factor within any PID loop
  #define DEFAULT_Kp 22.2
  #define DEFAULT_Ki 1.08
  #define DEFAULT_Kd 114
#define MAX_BED_POWER 255 // limits duty cycle to bed; 255=full current
  #define PID_FUNCTIONAL_RANGE 10 // If the temperature difference between the target temperature and the actual temperature
#define PREVENT_COLD_EXTRUSION
#define EXTRUDE_MINTEMP 170
#define PREVENT_LENGTHY_EXTRUDE
#define EXTRUDE_MAXLENGTH 200
#define THERMAL_PROTECTION_HOTENDS // Enable thermal protection for all extruders
#define THERMAL_PROTECTION_BED     // Enable thermal protection for the heated bed
#define THERMAL_PROTECTION_CHAMBER // Enable thermal protection for the heated chamber
#define COREXY
#define USE_XMIN_PLUG
#define USE_YMIN_PLUG
#define USE_ZMIN_PLUG
#define ENDSTOPPULLUPS
#define X_MIN_ENDSTOP_INVERTING false // Set to true to invert the logic of the endstop.
#define Y_MIN_ENDSTOP_INVERTING false // Set to true to invert the logic of the endstop.
#define Z_MIN_ENDSTOP_INVERTING true // Set to true to invert the logic of the endstop.
#define X_MAX_ENDSTOP_INVERTING false // Set to true to invert the logic of the endstop.
#define Y_MAX_ENDSTOP_INVERTING false // Set to true to invert the logic of the endstop.
#define Z_MAX_ENDSTOP_INVERTING false // Set to true to invert the logic of the endstop.
#define Z_MIN_PROBE_ENDSTOP_INVERTING true // Set to true to invert the logic of the probe.
#define DEFAULT_AXIS_STEPS_PER_UNIT   { 80, 80, 400, 127.323}
#define DEFAULT_MAX_FEEDRATE          { 600, 600, 10, 50 }
#define DEFAULT_MAX_ACCELERATION      { 3000, 3000, 100, 10000 }
#define DEFAULT_ACCELERATION          3000    // X, Y, Z and E acceleration for printing moves
#define DEFAULT_RETRACT_ACCELERATION  3000    // E acceleration for retracts
#define DEFAULT_TRAVEL_ACCELERATION   3000    // X, Y, Z acceleration for travel (non printing) moves
#define DEFAULT_EJERK    5.0  // May be used by Linear Advance
  #define JUNCTION_DEVIATION_MM 0.013 // (mm) Distance from real junction edge
  #define JD_HANDLE_SMALL_SEGMENTS    // Use curvature estimation instead of just the junction angle
#define Z_MIN_PROBE_USES_Z_MIN_ENDSTOP_PIN
#define NOZZLE_TO_PROBE_OFFSET { 10, 10, 0 }
#define PROBING_MARGIN 10
#define XY_PROBE_SPEED (133*60)
#define Z_PROBE_SPEED_FAST HOMING_FEEDRATE_Z
#define Z_PROBE_SPEED_SLOW (Z_PROBE_SPEED_FAST / 2)
#define Z_CLEARANCE_DEPLOY_PROBE   10 // Z Clearance for Deploy/Stow
#define Z_CLEARANCE_BETWEEN_PROBES  5 // Z Clearance between probe points
#define Z_CLEARANCE_MULTI_PROBE     5 // Z Clearance between multiple probes
#define Z_PROBE_LOW_POINT          -2 // Farthest distance below the trigger-point to go before stopping
#define Z_PROBE_OFFSET_RANGE_MIN -20
#define Z_PROBE_OFFSET_RANGE_MAX 20
#define X_ENABLE_ON 0
#define Y_ENABLE_ON 0
#define Z_ENABLE_ON 0
#define E_ENABLE_ON 0 // For all extruders
#define DISABLE_X false
#define DISABLE_Y false
#define DISABLE_Z false
#define DISABLE_E false             // Disable the extruder when not stepping
#define DISABLE_INACTIVE_EXTRUDER   // Keep only the active extruder enabled
#define INVERT_X_DIR true
#define INVERT_Y_DIR false
#define INVERT_Z_DIR false
#define INVERT_E0_DIR true
#define INVERT_E1_DIR false
#define INVERT_E2_DIR false
#define INVERT_E3_DIR false
#define INVERT_E4_DIR false
#define INVERT_E5_DIR false
#define INVERT_E6_DIR false
#define INVERT_E7_DIR false
#define X_HOME_DIR -1
#define Y_HOME_DIR -1
#define Z_HOME_DIR -1
#define X_BED_SIZE 220
#define Y_BED_SIZE 220
#define X_MIN_POS 0
#define Y_MIN_POS 0
#define Z_MIN_POS 0
#define X_MAX_POS X_BED_SIZE
#define Y_MAX_POS Y_BED_SIZE
#define Z_MAX_POS 220
#define MIN_SOFTWARE_ENDSTOPS
  #define MIN_SOFTWARE_ENDSTOP_X
  #define MIN_SOFTWARE_ENDSTOP_Y
  #define MIN_SOFTWARE_ENDSTOP_Z
#define MAX_SOFTWARE_ENDSTOPS
  #define MAX_SOFTWARE_ENDSTOP_X
  #define MAX_SOFTWARE_ENDSTOP_Y
  #define MAX_SOFTWARE_ENDSTOP_Z
#define HOMING_FEEDRATE_XY (50*60)
#define HOMING_FEEDRATE_Z  (4*60)
#define VALIDATE_HOMING_ENDSTOPS
#define EEPROM_SETTINGS     // Persistent storage with M500 and M501
#define EEPROM_CHITCHAT       // Give feedback on EEPROM commands. Disable to save PROGMEM.
#define EEPROM_BOOT_SILENT    // Keep M503 quiet and only give errors during first load
  #define EEPROM_AUTO_INIT  // Init EEPROM automatically on any errors.
#define HOST_KEEPALIVE_FEATURE        // Disable this if your host doesn't like keepalive messages
#define DEFAULT_KEEPALIVE_INTERVAL 2  // Number of seconds between "busy" messages. Set with M113.
#define BUSY_WHILE_HEATING            // Some hosts require "busy" messages even during heating
#define PREHEAT_1_LABEL       "PLA"
#define PREHEAT_1_TEMP_HOTEND 210
#define PREHEAT_1_TEMP_BED     60
#define PREHEAT_1_FAN_SPEED     0 // Value from 0 to 255
#define PREHEAT_2_LABEL       "ABS"
#define PREHEAT_2_TEMP_HOTEND 240
#define PREHEAT_2_TEMP_BED    110
#define PREHEAT_2_FAN_SPEED     0 // Value from 0 to 255
#define PRINTJOB_TIMER_AUTOSTART
#define LCD_LANGUAGE zh_CN
#define DISPLAY_CHARSET_HD44780 JAPANESE
#define LCD_INFO_SCREEN_STYLE 0
#define SDSUPPORT
#define INDIVIDUAL_AXIS_HOMING_MENU
#define REPRAP_DISCOUNT_FULL_GRAPHIC_SMART_CONTROLLER
#define SOFT_PWM_SCALE 0
#define SERVO_DELAY { 300 }

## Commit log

2021-08-11 hbot
    v2.1
    [.DWG, 12864显示屏.DWG, 12864显示屏.SLDPRT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]
2021-08-15 hbot
    hbot
    [丝杆固定2.SLDPRT, 丝杆固定2.STL, 装配体1.SLDASM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]

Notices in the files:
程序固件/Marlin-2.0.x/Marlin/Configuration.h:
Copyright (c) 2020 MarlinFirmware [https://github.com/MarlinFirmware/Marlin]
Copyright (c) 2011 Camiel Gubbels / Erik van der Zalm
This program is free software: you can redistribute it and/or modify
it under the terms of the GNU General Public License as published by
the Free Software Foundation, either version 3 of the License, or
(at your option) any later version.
